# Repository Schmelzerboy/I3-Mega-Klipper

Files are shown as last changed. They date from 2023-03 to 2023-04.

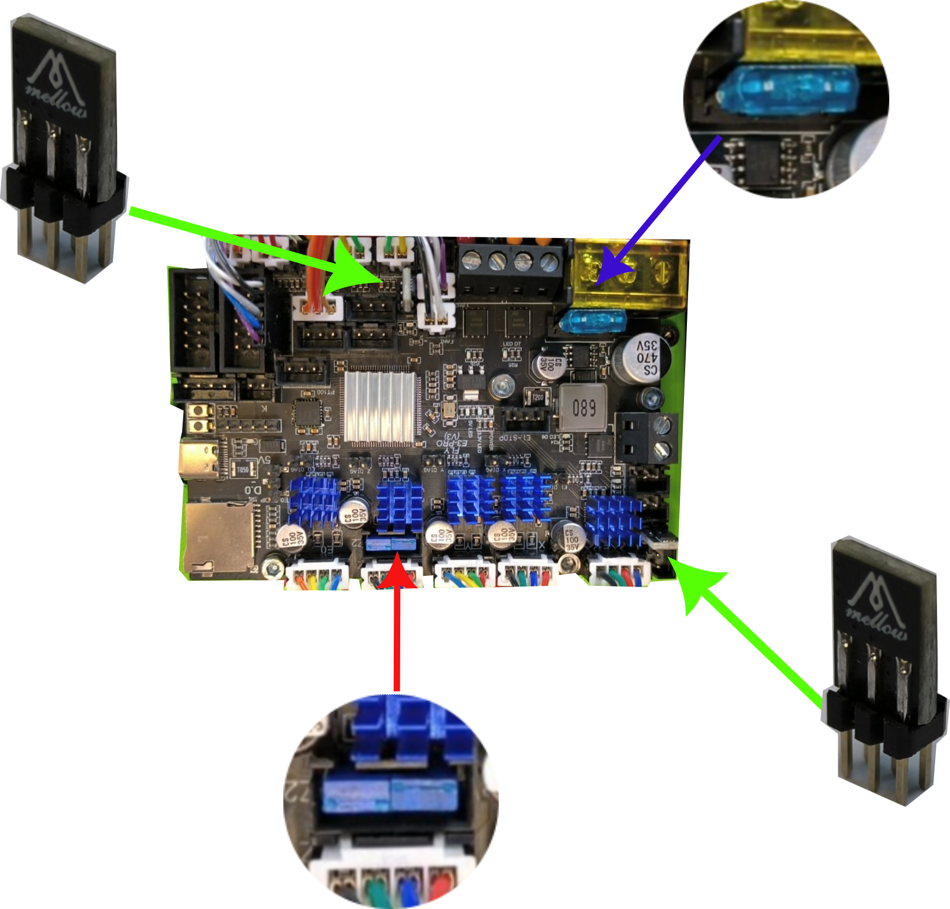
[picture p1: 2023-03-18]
Wireing Schaltplaene/Hardware_Board.png

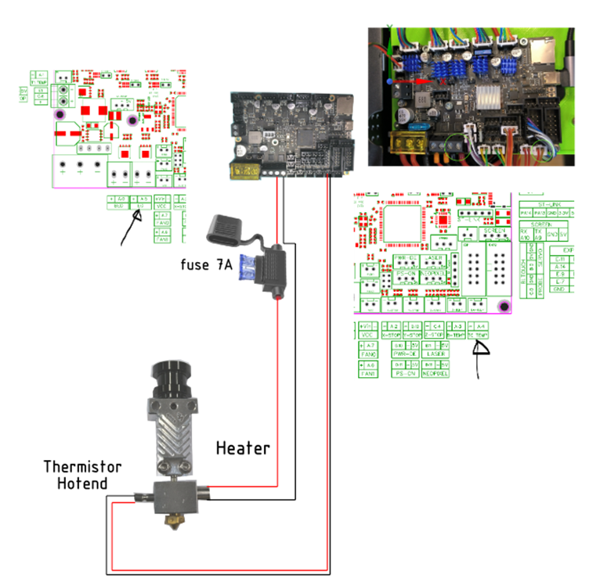
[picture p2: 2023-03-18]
Wireing Schaltplaene/hotend.PNG

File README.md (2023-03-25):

#  Anycubic I3Mega Tuning Mainsail + Klipper feat. @dr.klipper 

Video Links:  
Part 1 - https://youtu.be/kW5aFmzocZc (Anycubic I3Mega Tuning Teil 13 Mainsail + Klipper feat. @dr.klipper)  
Part 2 - https://youtu.be/CcnwJQRyG4Y (#46 - Klipper FAQ - komplette Installation)  
Part 3 - TBD

Kanal von Dr. Klipper:  
https://www.youtube.com/@dr.klipper

Mein Kanal:  
https://www.youtube.com/channel/UCTYNFDNzhLzgfR8x1OPZsGg

Mega Tuning Serie https://www.youtube.com/playlist?list=PLIsc8b5bFDG1j1bmuFCcvaNI3M9-2phBW

alle anderen Projekte:
https://www.thingiverse.com/schmelzerboy/designs

### Warnung : Ich übernehme keine Verantwortung für Schäden an Menschen oder Maschine. Der Einbau erfolgt auf eigene Gefahr. Nach Deutschen Recht dürfen nicht Elektiker keine Arbeiten an 230 Volt Netzen durchführen!

Es gelten die 5 Sicherheitsregeln:  

- Freischalten. Als Freischalten bezeichnet man das allpolige Trennen einer elektrischen Anlage von spannungsführenden Teilen.  
- Gegen Wiedereinschalten sichern.  
- Spannungsfreiheit feststellen.  
- Erden und Kurzschließen.  
- Benachbarte, unter Spannung stehende Teile abdecken oder abschranken.  

### Warning : I take no responsibility for any damage to people or machine. Installation is at your own risk. According to German law, non-electricians are not allowed to work on 230 volt networks!

The 5 safety rules apply:  

- Unlock. Disconnecting is the all-pole disconnection of an electrical system from live parts. ...
- Secure against being switched on again. ...
- determine the absence of tension. ...
- grounding and short-circuiting. ...
- Cover or fence off adjacent live parts.

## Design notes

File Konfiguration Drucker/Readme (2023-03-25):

Download:
https://github.com/Schmelzerboy/I3-Mega-Klipper

Schmelzerboy YT Kanal:
https://www.youtube.com/channel/UCTYNFDNzhLzgfR8x1OPZsGg

Dr. Klipper YT Kanal:
https://www.youtube.com/@dr.klipper

## Video Links
#> Part 1 - https://youtu.be/kW5aFmzocZc (Anycubic I3Mega Tuning Teil 13 Mainsail + Klipper feat. @dr.klipper)
#> Part 2 - https://youtu.be/CcnwJQRyG4Y (#46 - Klipper FAQ - komplette Installation)
#> Part 3 - TBD

Hier ist die Printer.cfg und Macros.cfg

Config ist mit folgenden Optionen

- BL Touch
- Mellow E3 Pro Board
- Neo Pixel
- 3 Lüfter / Hotend / Bauteillüter / Board Lüfter

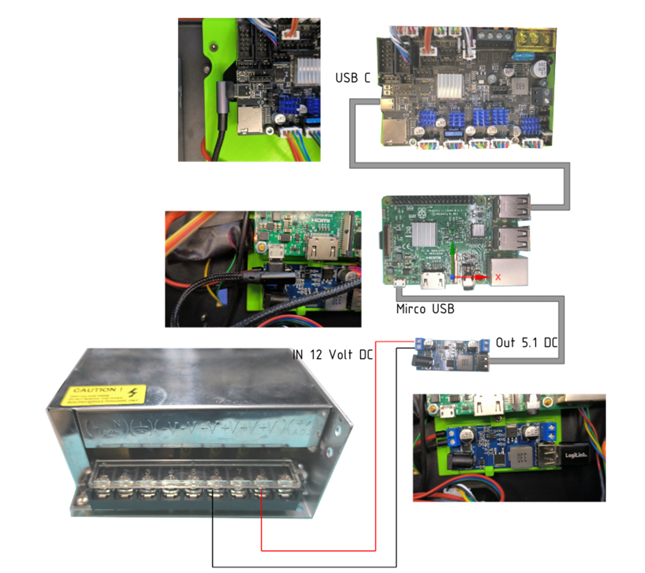
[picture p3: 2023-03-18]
Wireing Schaltplaene/DCDCWAndler.png

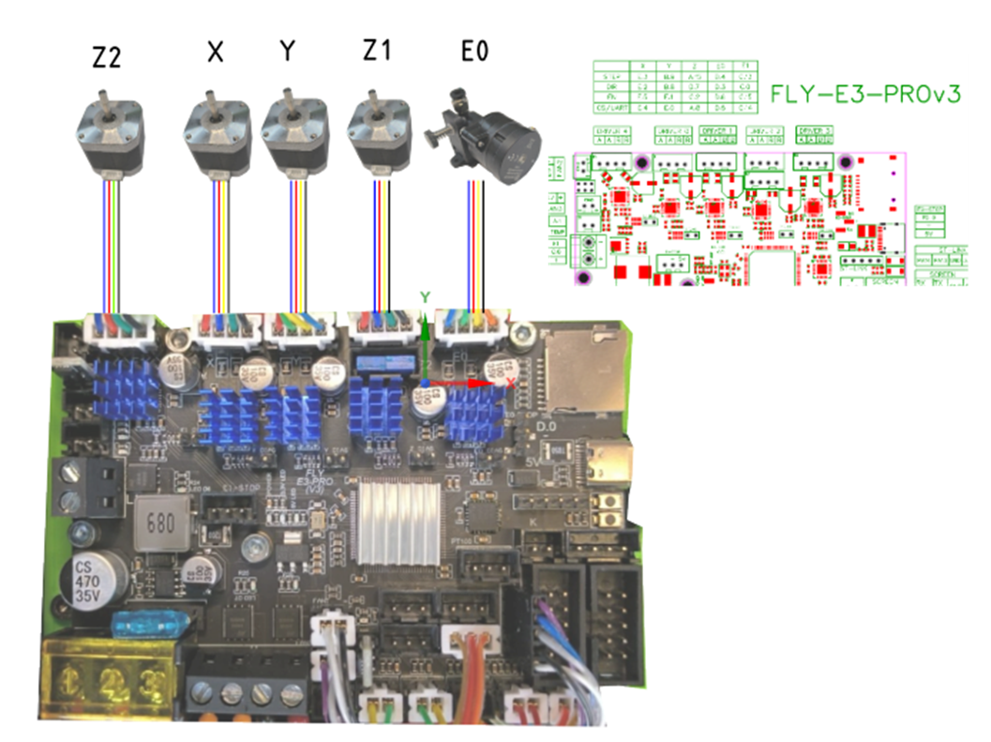
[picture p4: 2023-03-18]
Wireing Schaltplaene/Stepper.png

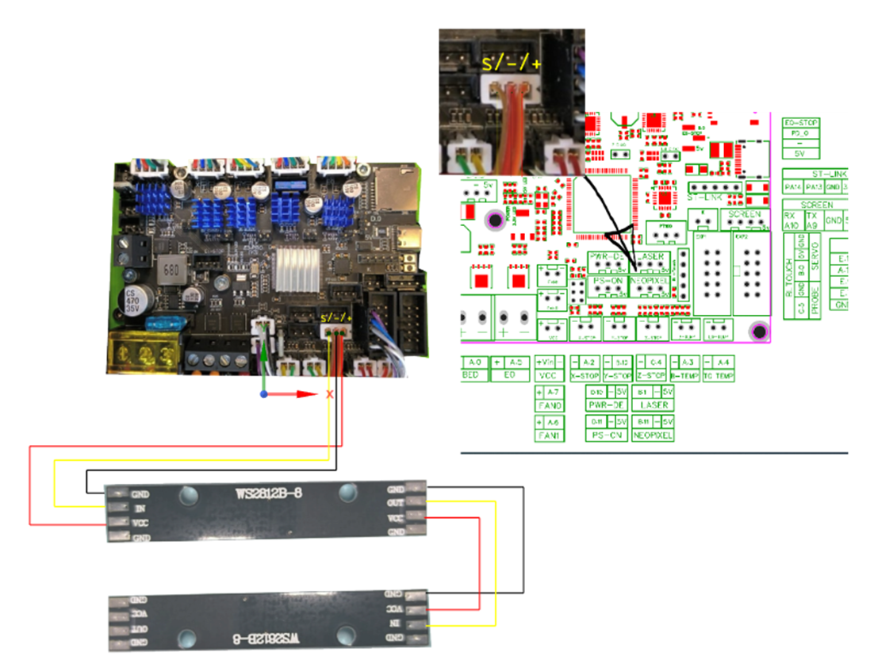
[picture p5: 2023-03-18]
Wireing Schaltplaene/neopixel.png

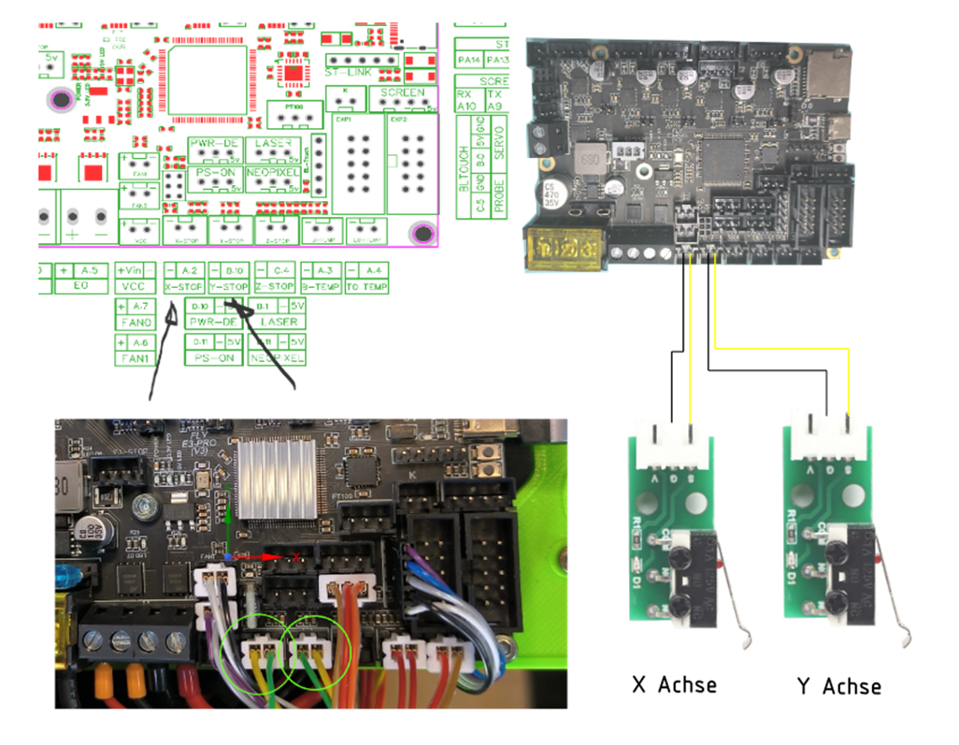
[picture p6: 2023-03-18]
Wireing Schaltplaene/Endstops.png

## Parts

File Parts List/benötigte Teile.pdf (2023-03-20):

===== Benötigte Teile =====

**NF Zone V6 12 Volt**

https://meltbro.de/nf-zone-cr10-hotend-optimiertes-hotend-fuer-ender-3-ender-5-cr-10-v6-hotend.html

**Gutscheincode "schmelzerboy"**

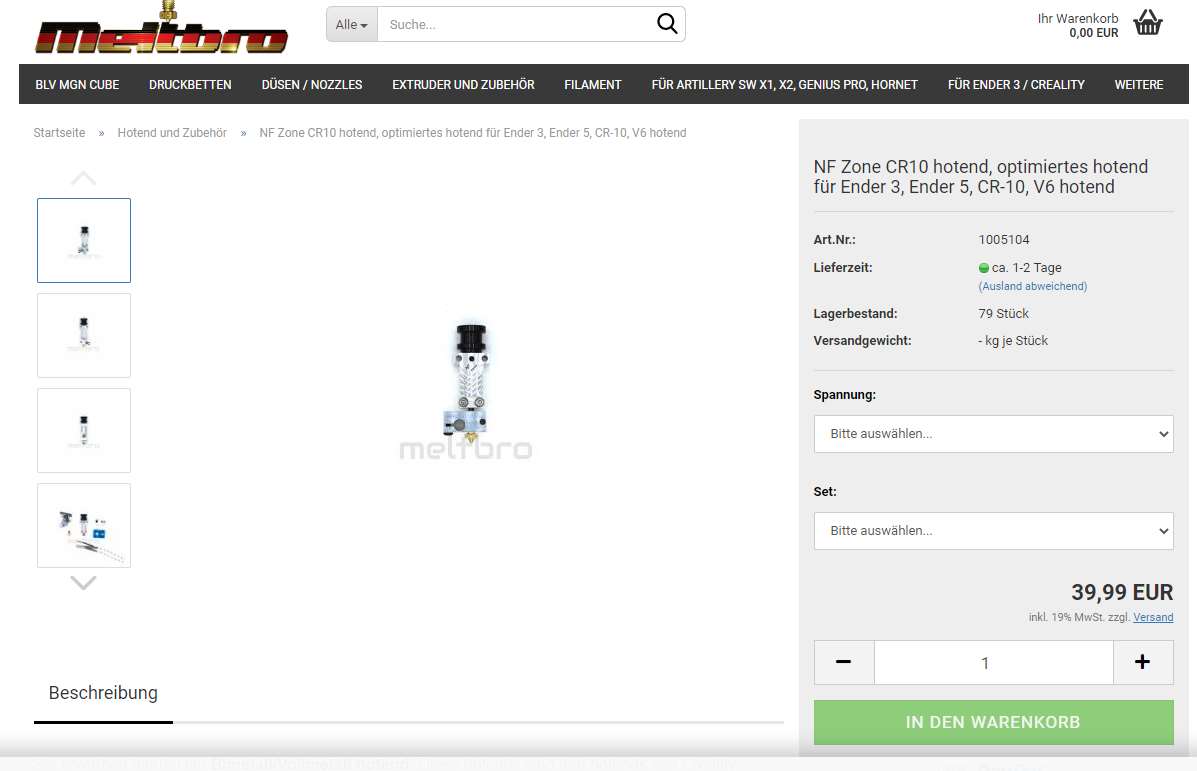
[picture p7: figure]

**Original BL Touch Sensor Nivellierung V3.1**

https://meltbro.de/original-bl-touch-nivellierungssensor-v3-1-hohe-praezision-ender-3-diydrucker.html

**Gutscheincode "schmelzerboy"**

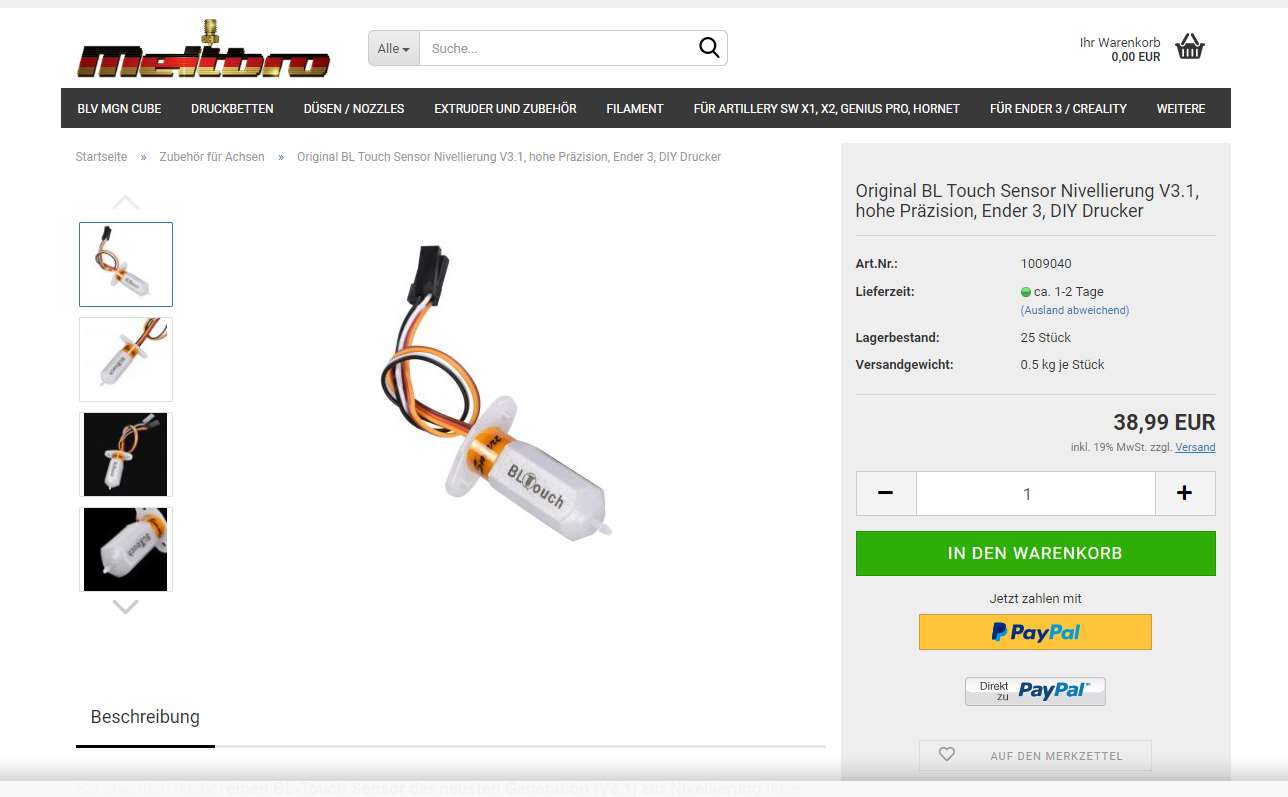
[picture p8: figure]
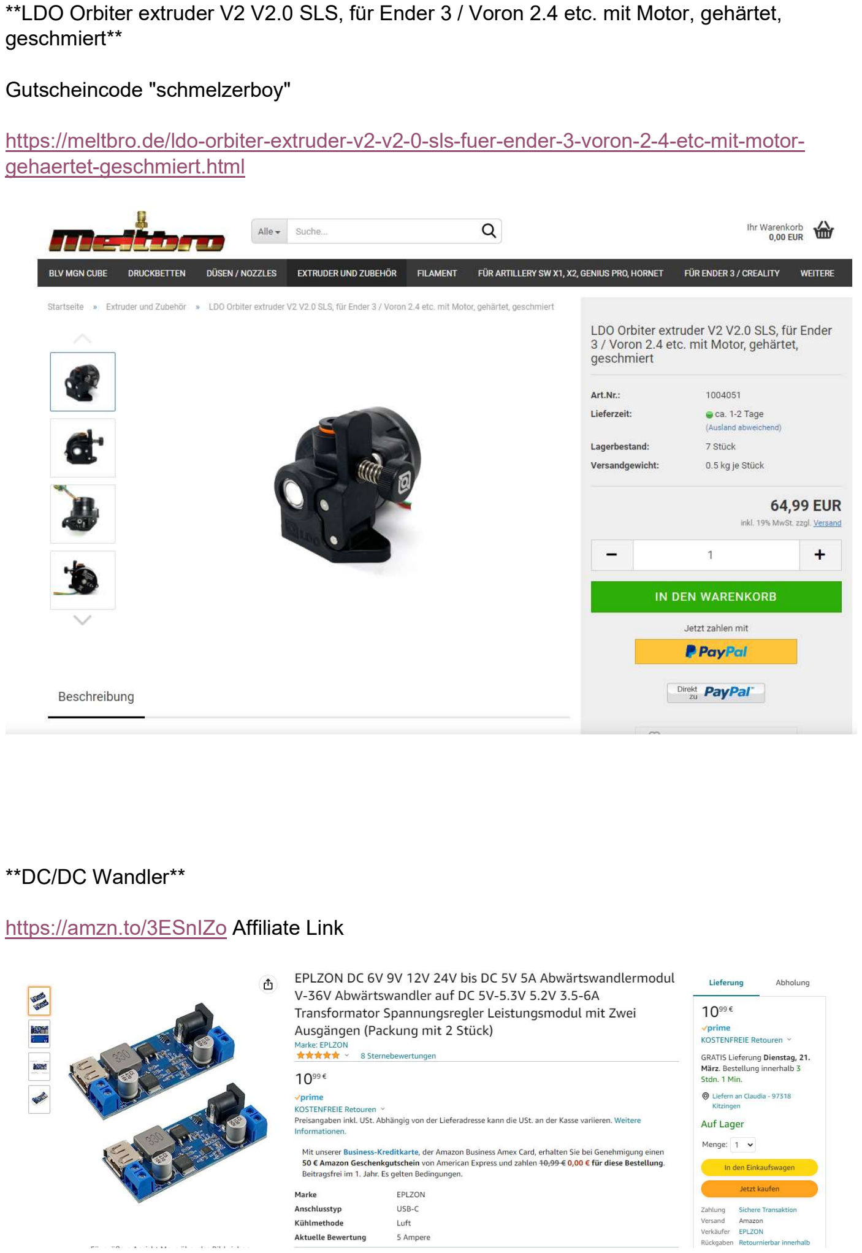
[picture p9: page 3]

**LDO Orbiter extruder V2 V2.0 SLS, für Ender 3 / Voron 2.4 etc. mit Motor, gehärtet, geschmiert**

Gutscheincode "schmelzerboy"

https://meltbro.de/ldo-orbiter-extruder-v2-v2-0-sls-fuer-ender-3-voron-2-4-etc-mit-motorgehaertet-geschmiert.html

**DC/DC Wandler**

https://amzn.to/3ESnIZo Affiliate Link

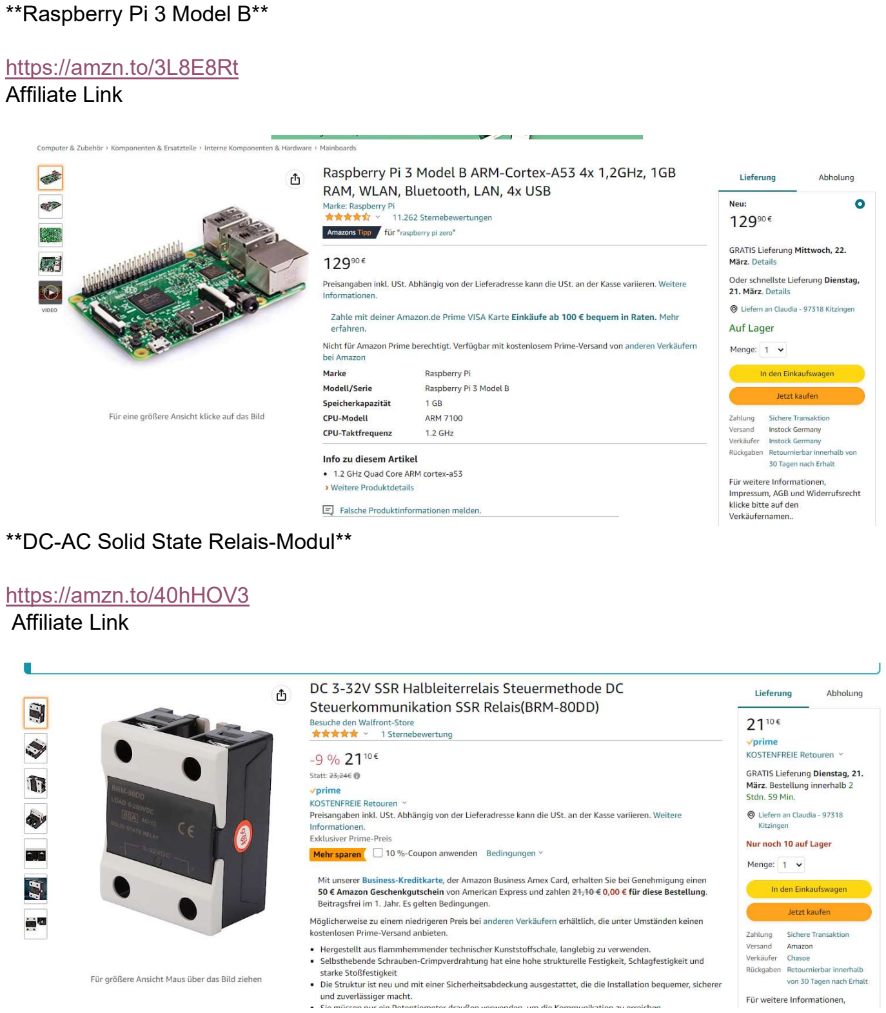
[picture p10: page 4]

**Raspberry Pi 3 Model B**

https://amzn.to/3L8E8Rt
Affiliate Link

**DC-AC Solid State Relais-Modul**

https://amzn.to/40hHOV3
Affiliate Link

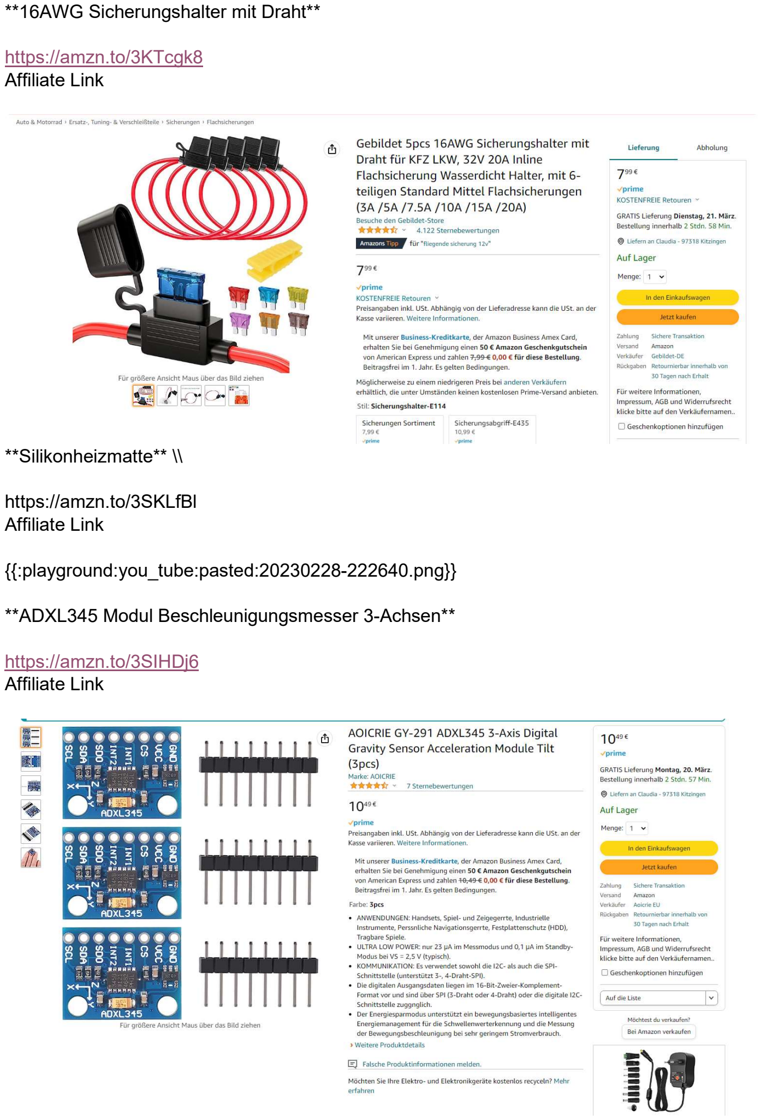
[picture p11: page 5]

**16AWG Sicherungshalter mit Draht**

https://amzn.to/3KTcgk8
Affiliate Link

**Silikonheizmatte** \\

https://amzn.to/3SKLfBl
Affiliate Link

{{:playground:you_tube:pasted:20230228-222640.png}}

**ADXL345 Modul Beschleunigungsmesser 3-Achsen**

https://amzn.to/3SIHDj6
Affiliate Link

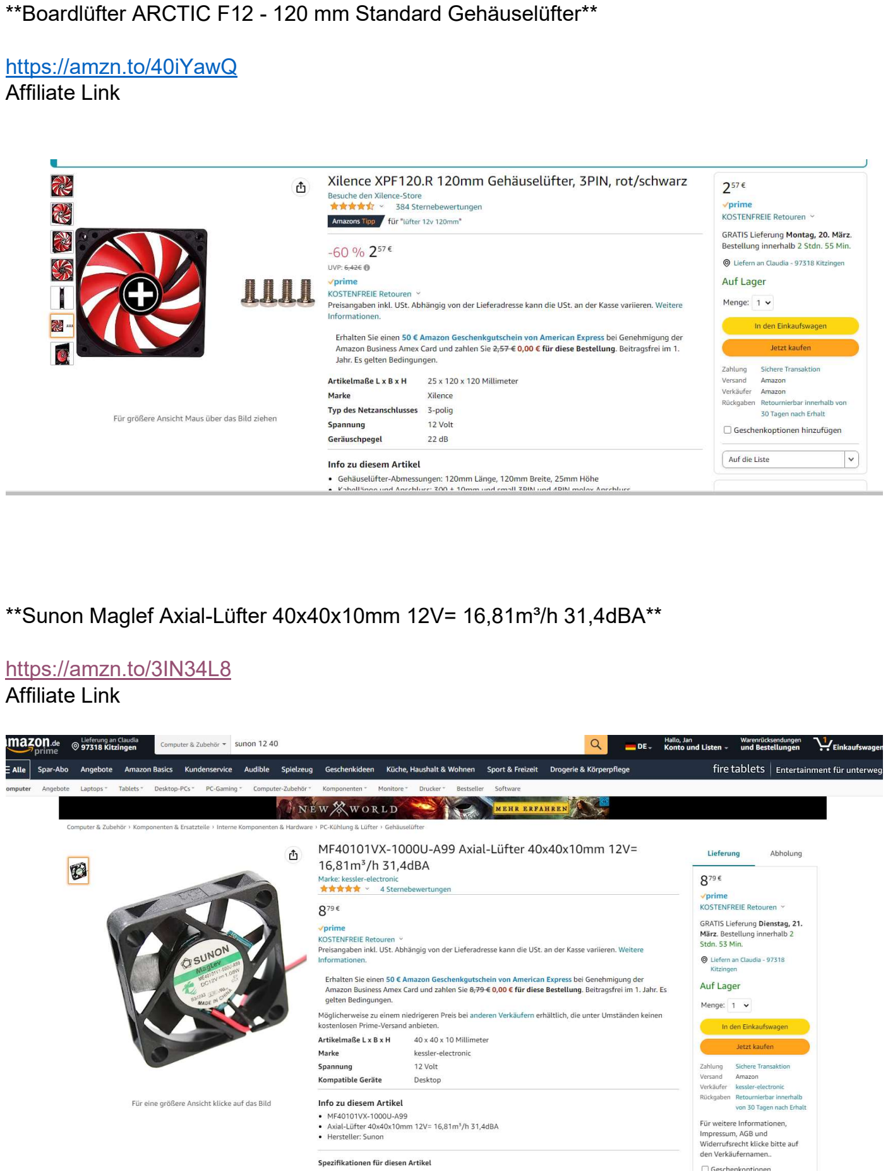
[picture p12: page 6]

**Boardlüfter ARCTIC F12 - 120 mm Standard Gehäuselüfter**

https://amzn.to/40iYawQ
Affiliate Link

**Sunon Maglef Axial-Lüfter 40x40x10mm 12V= 16,81m³/h 31,4dBA**

https://amzn.to/3IN34L8
Affiliate Link

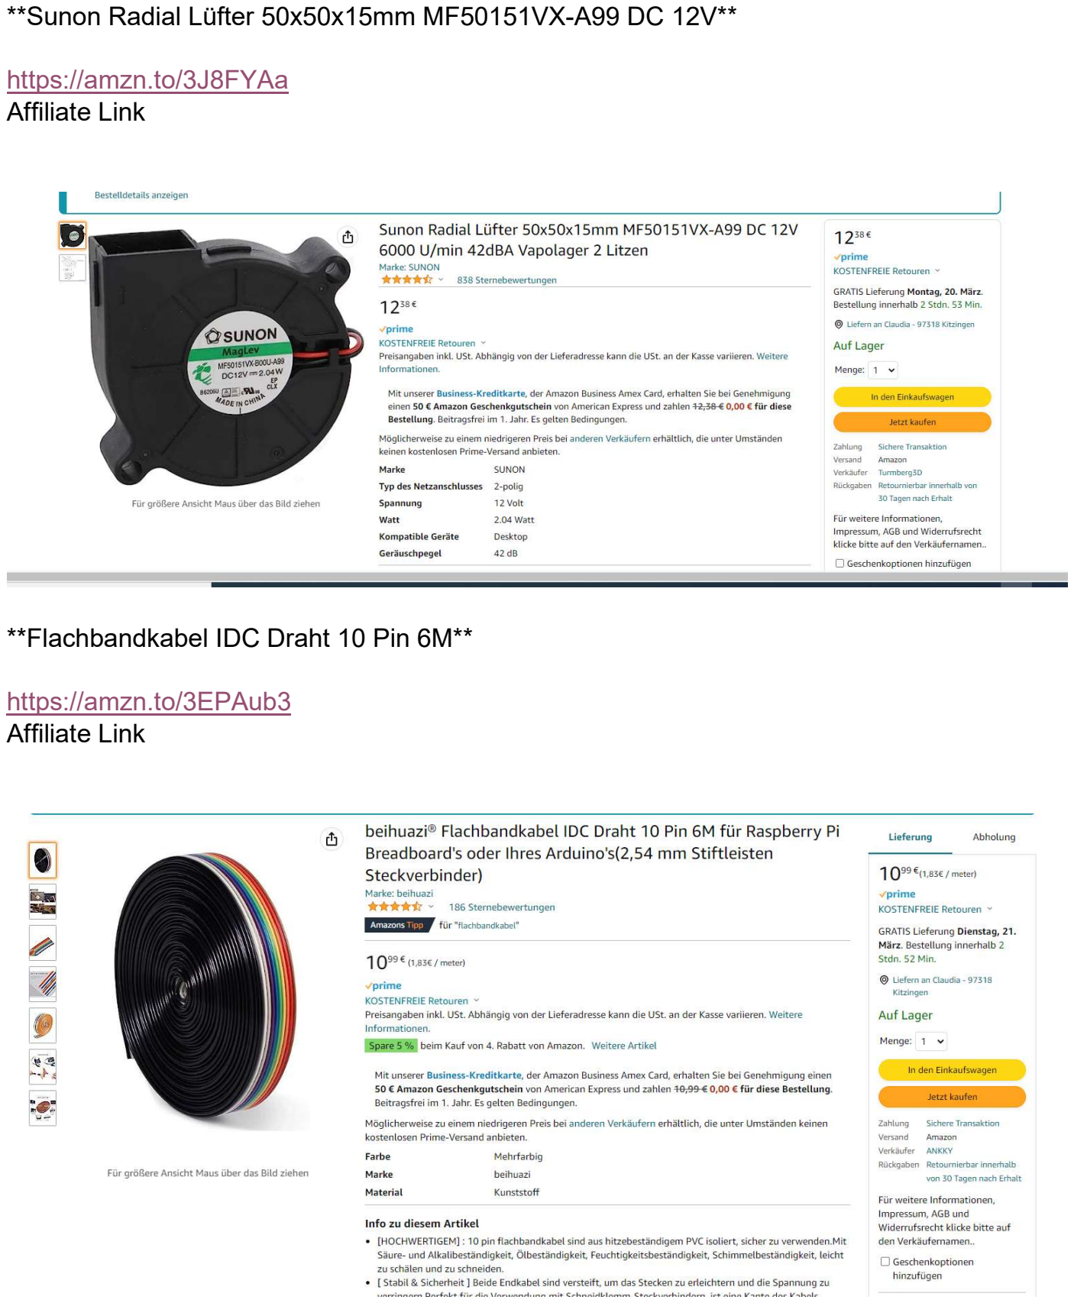
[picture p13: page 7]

**Sunon Radial Lüfter 50x50x15mm MF50151VX-A99 DC 12V**

https://amzn.to/3J8FYAa
Affiliate Link

**Flachbandkabel IDC Draht 10 Pin 6M**

https://amzn.to/3EPAub3
Affiliate Link

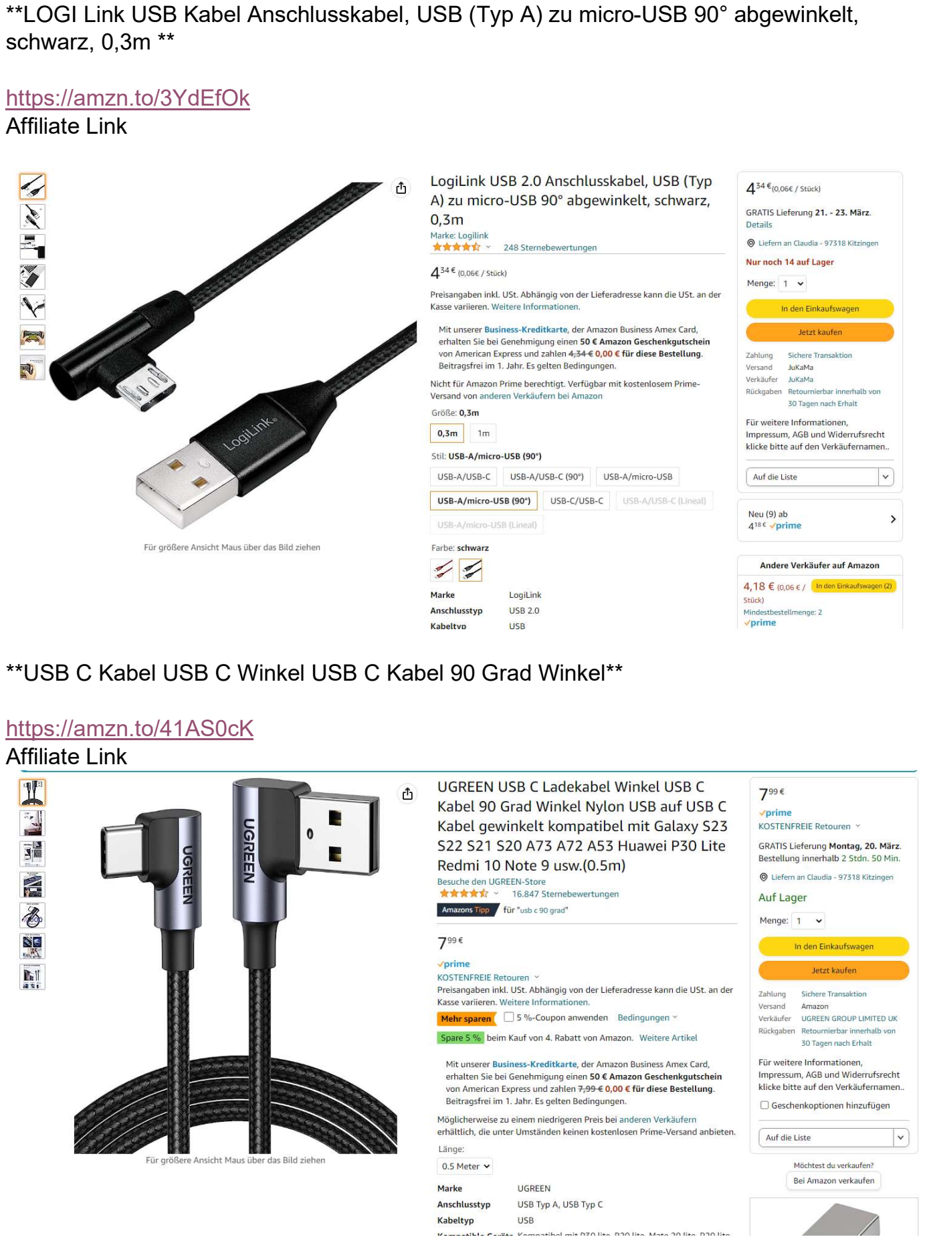
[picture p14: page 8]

**LOGI Link USB Kabel Anschlusskabel, USB (Typ A) zu micro-USB 90° abgewinkelt, schwarz, 0,3m **

https://amzn.to/3YdEfOk
Affiliate Link

**USB C Kabel USB C Winkel USB C Kabel 90 Grad Winkel**

https://amzn.to/41AS0cK
Affiliate Link

**Schrittmotorkabel 1000mm Stepper Motor Kabel**

https://amzn.to/3yPMzcP
Affiliate Link


**Heat Shrink Tubing Electric / Schrumpfschlauch**

https://amzn.to/3mfk7xX


**Werkzeug**

**Crimpzange Dupont Stecker Set - Preciva 1550 pcs 2,54 mm**

https://amzn.to/3ZCbo7h
Affiliate Link

**Lötkolben**
Affiliate Link

https://amzn.to/3IJ1Pgk


**Lötzinn**

https://amzn.to/3ZVIGPF
Affiliate Link

**Voltmeter**

https://amzn.to/3mnKEcm
Affiliate Link


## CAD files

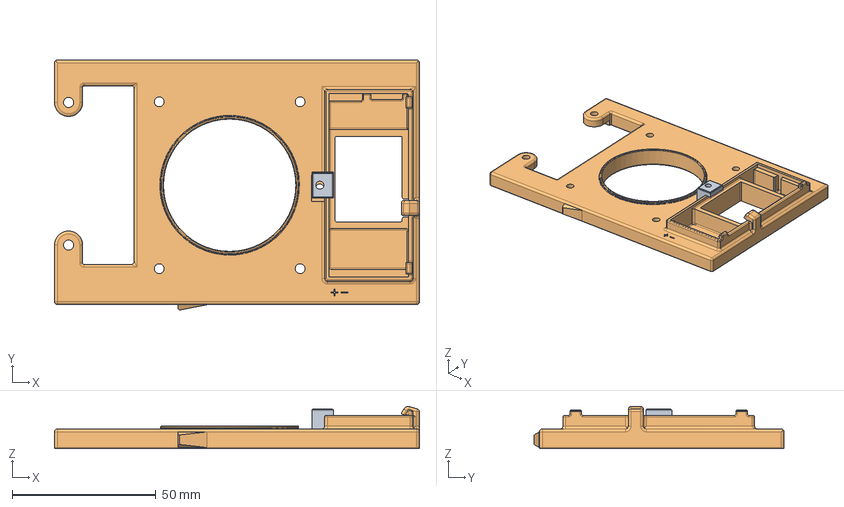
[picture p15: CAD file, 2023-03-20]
STL STEP/Pi_SSR.stp
126.9 x 87.0 x 14.6 mm
Komponente4
Volumenkörper

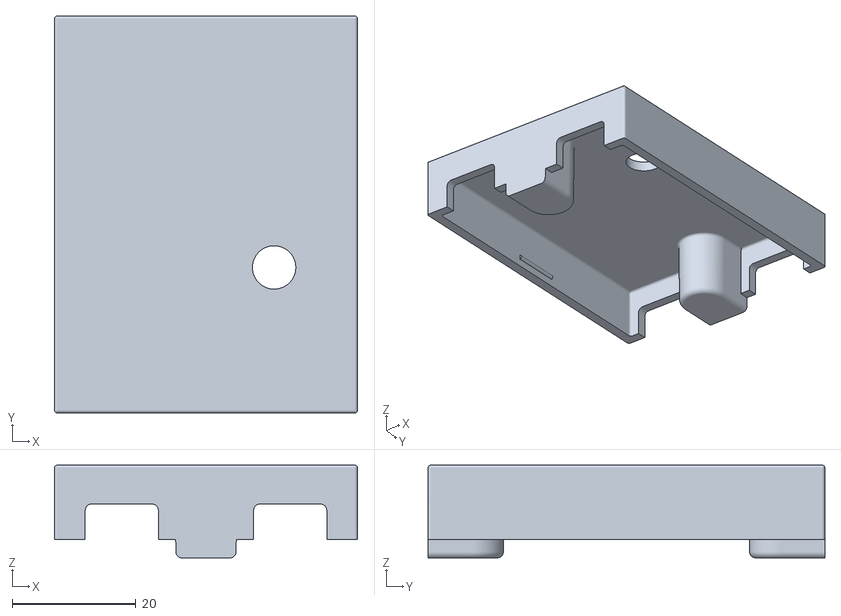
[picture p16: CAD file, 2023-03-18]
STL STEP/ssr cover.stl
49.0 x 64.1 x 15.0

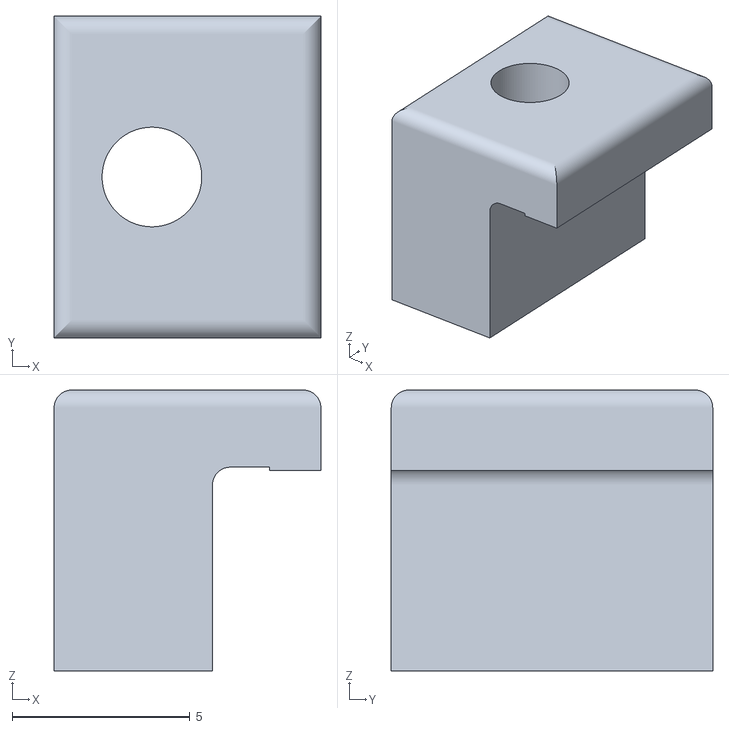
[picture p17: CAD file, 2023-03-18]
STL STEP/Pi_SSR_pusher.stl
7.50 x 9.04 x 7.90

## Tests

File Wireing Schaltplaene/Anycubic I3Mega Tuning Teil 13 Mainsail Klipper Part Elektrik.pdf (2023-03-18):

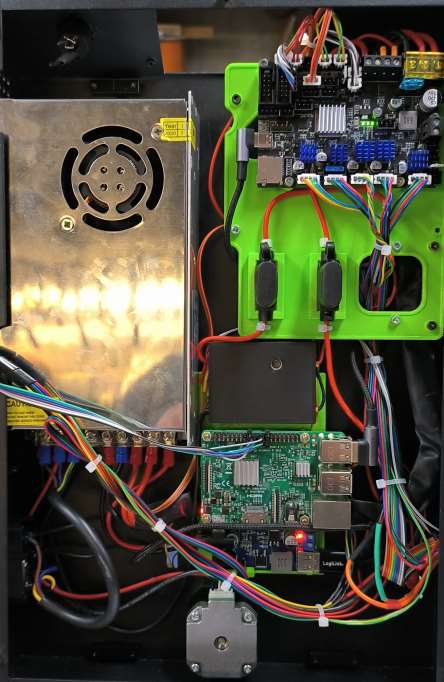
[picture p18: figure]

Download at: https://github.com/Schmelzerboy/I3-Mega-Klipper

### 1 Schmelzdoku Mainsail Klipper

# Anycubic I3Mega Tuning Teil 13 Mainsail Klipper Part: Elektrik

Warning : I take no responsibility for any damage to people or machine. The installation takes place at risk.
Warung : Ich übernehme keine Verantwortung für Schäden an Menschen oder Maschine. Der Einbau erfolgt auf eigene Gefahr.

### 2 Schmelzdoku Mainsail Klipper

Board Mellow E3 ProV3 Doku:

https://teamgloomy.github.io/fly_e3_pro_v3_general.html

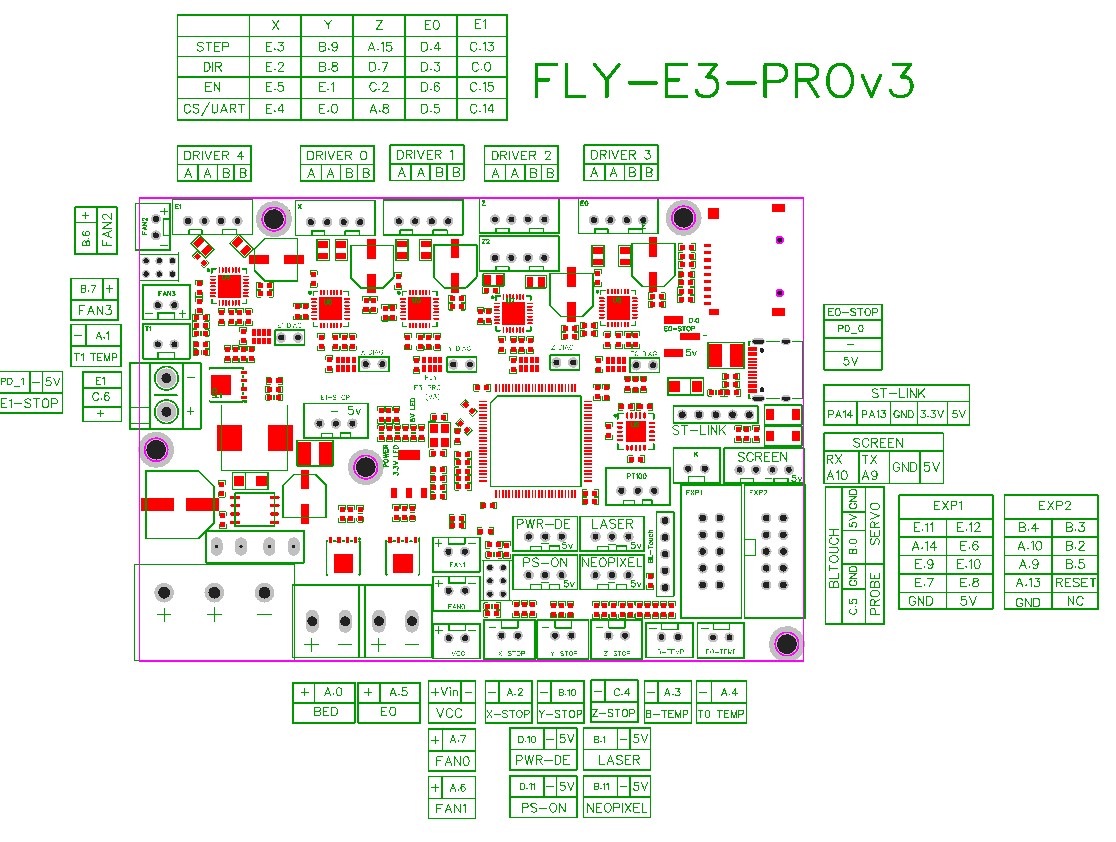
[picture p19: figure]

### 3 Schmelzdoku Mainsail Klipper

### 1. Board Settings

- blue 10A fuse
- green fan mosfet
- red jumper Z- Axis

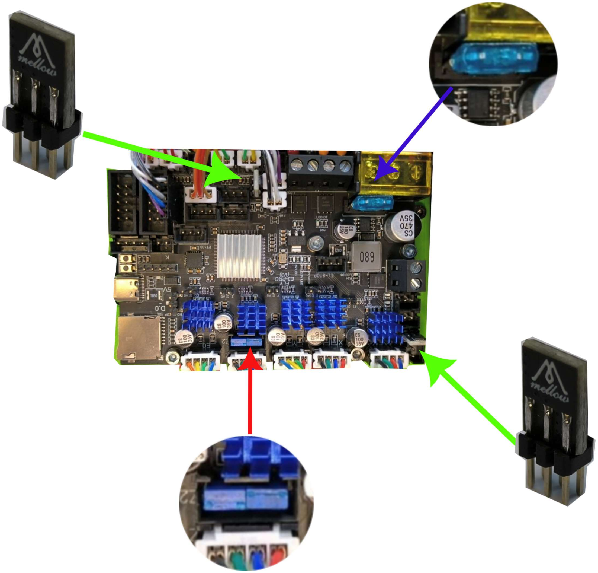
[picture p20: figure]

2. [fan]

### 4 Schmelzdoku Mainsail Klipper

- Fan 0 pin: PA7 [fan]
- Fan 1 pin: PA6 [heater fan]
- Fan 3 pin: PB7 [controller_fan]

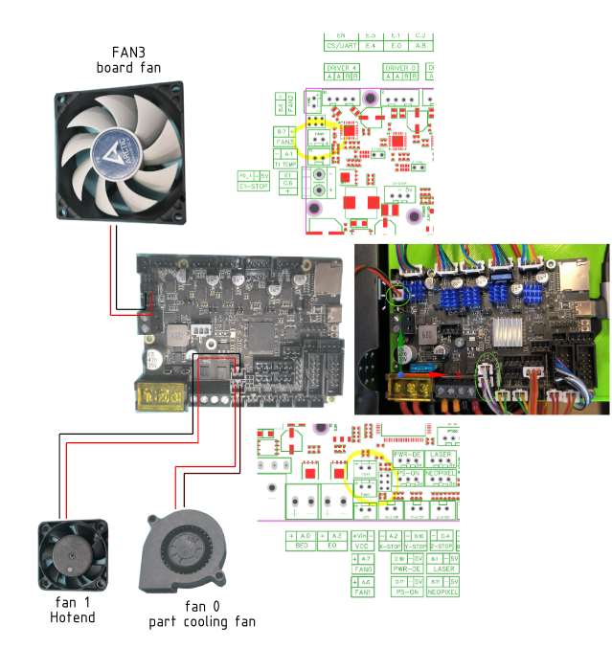
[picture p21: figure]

### 3. Power Supply Board

### 5 Schmelzdoku Mainsail Klipper

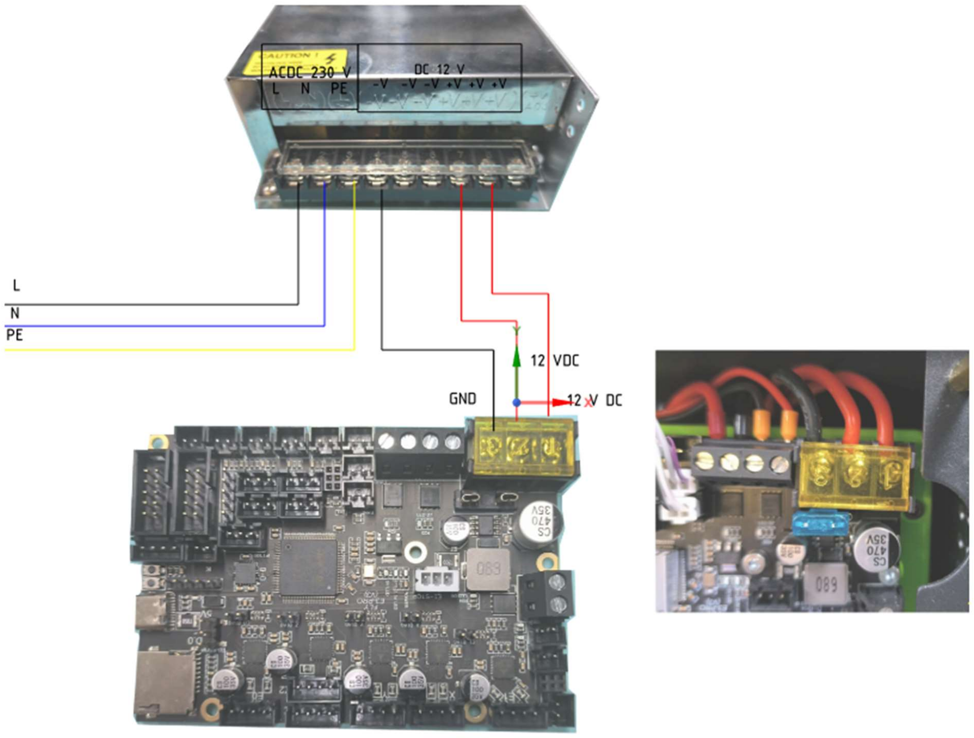
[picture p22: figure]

4. [heater_bed]

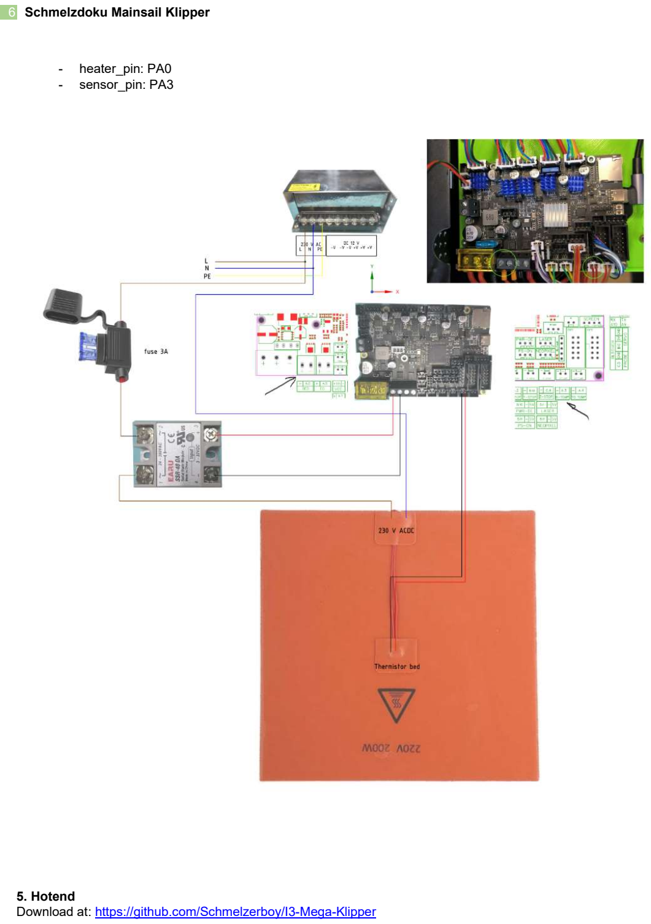
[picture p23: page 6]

### 6 Schmelzdoku Mainsail Klipper

- heater_pin: PA0
- sensor_pin: PA3

### 5. Hotend

### 7 Schmelzdoku Mainsail Klipper

heater_pin: PA5
sensor_pin: PA4

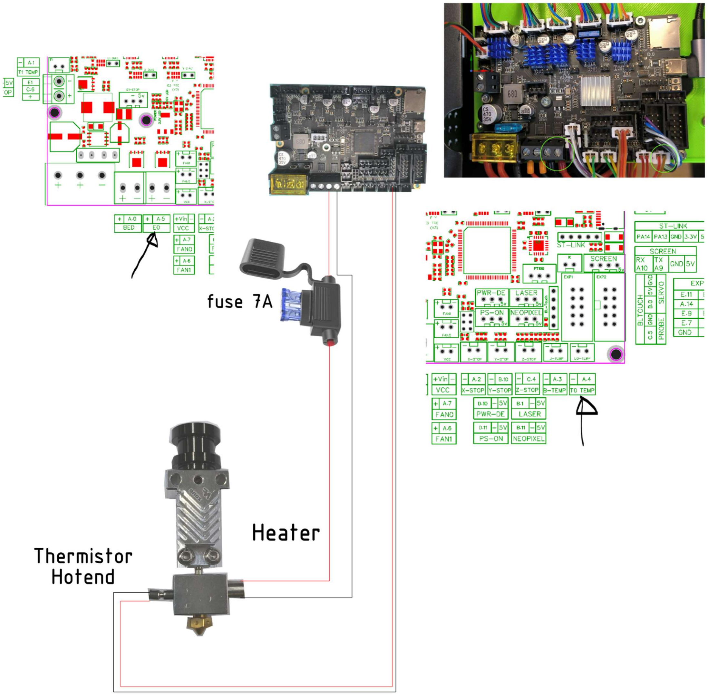
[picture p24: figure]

### 6. Stepper

### 8 Schmelzdoku Mainsail Klipper

[stepper_x] | step_pin: PE3 dir_pin: PE2 enable_pin: !PE5
[stepper_y] | step_pin: PB3 dir_pin: PB8 enable_pin: !PE1
[stepper_z] | step_pin: PA15 dir_pin: PD7 enable_pin: !PC2
[stepper_z1] | step_pin: PC13 dir_pin: PC0 enable_pin: !PC15
[extruder] | step_pin: PD4 dir_pin: PD3 enable_pin: !PD6

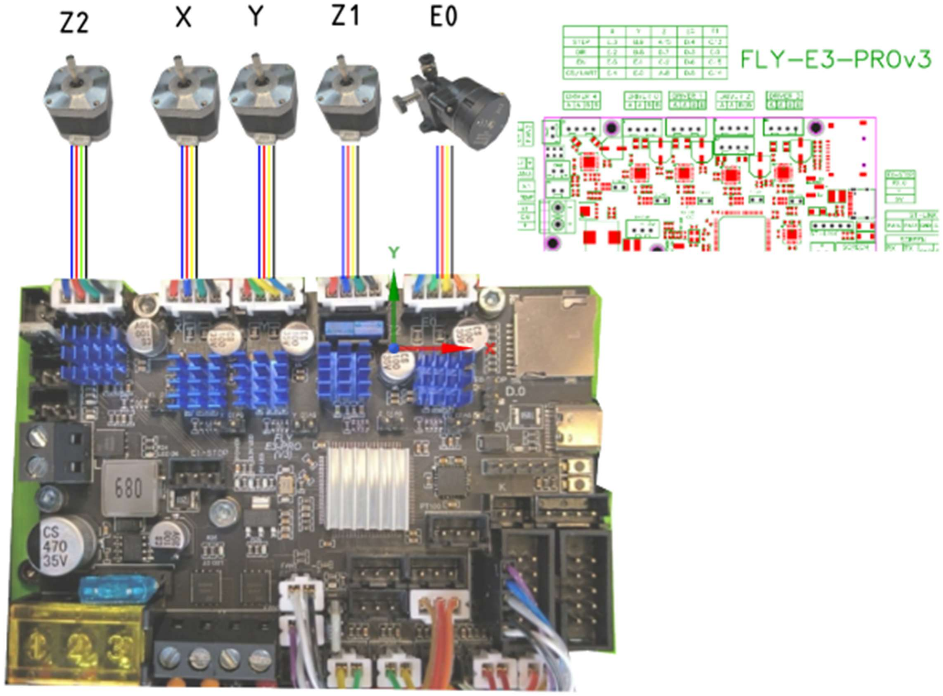
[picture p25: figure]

6. [bltouch]

### 9 Schmelzdoku Mainsail Klipper

sensor_pin: ^PC5
control_pin: PB0

Check:
https://teamgloomy.github.io/fly_e3_pro_v3_bltouch.html

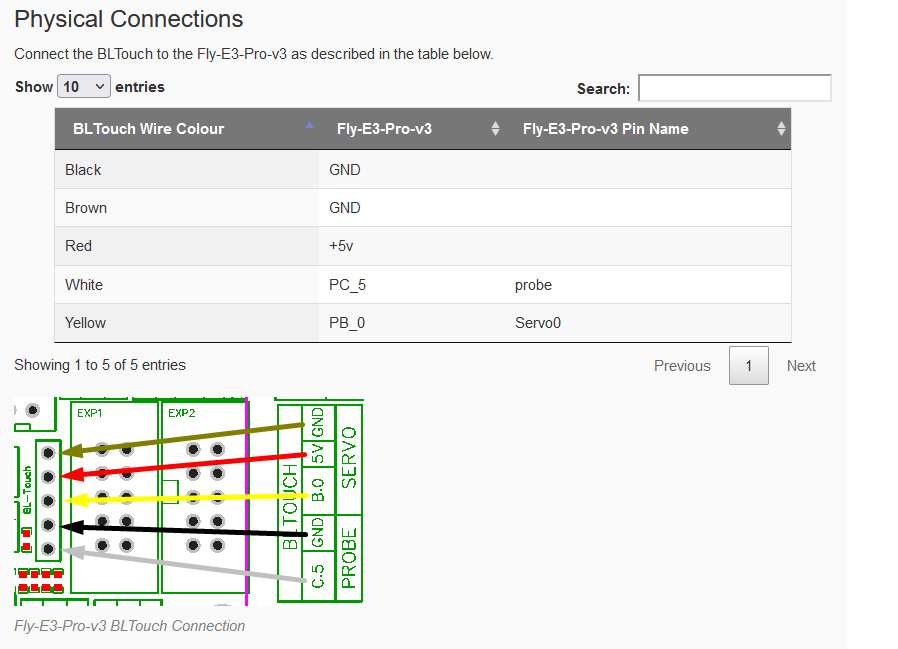
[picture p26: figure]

### 7. Endstops

### 10 Schmelzdoku Mainsail Klipper

X = endstop_pin: !PA2
Y= endstop_pin: !PB10

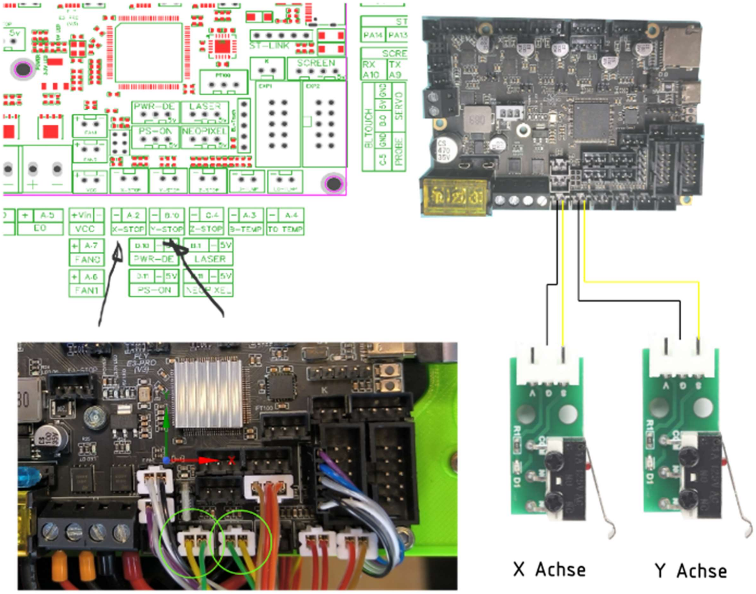
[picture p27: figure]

### 11 Schmelzdoku Mainsail Klipper

8. [ADXL]

cs_pin: rpi:None

9 . DC/DC Wandler / USB Verkabelung


### 12 Schmelzdoku Mainsail Klipper

10. [neopixel Leds]


### 13 Schmelzdoku Mainsail Klipper

pin : PB11

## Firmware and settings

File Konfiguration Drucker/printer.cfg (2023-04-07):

## Master Link für alle Anleitungen / Printer.cfg / macros:
## https://github.com/Schmelzerboy/I3-Mega-Klipper
##
## Printer Anycuic I3 Mega MK4 THE REAL ORBITER KLIPPER Version
# Projekt wurde erstellt von:
#  Jan Oerter      (YT Schmelzerboy) ###https://www.youtube.com/channel/UCTYNFDNzhLzgfR8x1OPZsGg
#  Dominik Schmidt (YT Dr. KLipper)  ###https://www.youtube.com/@dr.klipper

## Default Compile Settings
#> CanBoot (https://github.com/Arksine/CanBoot)
#      Micro-controller Architecture (STMicroelectronics STM32)  --->
#      Processor model (STM32F407)  --->
#      Build CanBoot deployment application (32KiB bootloader)  --->
#      Clock Reference (8 MHz crystal)  --->
#      Communication interface (USB (on PA11/PA12))  --->
#      Application start offset (32KiB offset)  --->
#      USB ids  --->
#  ()  GPIO pins to set on bootloader entry
#  [*] Support bootloader entry on rapid double click of reset button
#  [ ] Enable bootloader entry on button (or gpio) state
#  [ ] Enable Status LED
#
#> Klipper 
#  [*] Enable extra low-level configuration options
#      Micro-controller Architecture (STMicroelectronics STM32)  --->
#      Processor model (STM32F407)  --->
#      Bootloader offset (32KiB bootloader)  --->
#      Clock Reference (8 MHz crystal)  --->
#      Communication interface (USB (on PA11/PA12))  --->
#      USB ids  --->
#  ()  GPIO pins to set at micro-controller startup

## Video Links
## Installation / Einrichtung
#> Part 1 - https://youtu.be/kW5aFmzocZc (Anycubic I3Mega Tuning Teil 13 Mainsail + Klipper feat. @dr.klipper)
#> Part 2 - https://youtu.be/CcnwJQRyG4Y (#46 - Klipper FAQ - komplette Installation)
#> Part 3 - TBD

#> Demo Video:
##> https://youtu.be/m_DZtZd5RRo (Anycubic I3 Mega "Der Einstiegsdrucker" kann 30 min. Benchy drucken?)

## Wichtige Links:
## Mellow FLY-E3 Pro V3:
## Pinout E3 Pro V3 https://teamgloomy.github.io/fly_e3_pro_v3_pins.html
## Ellis Prining Guide:
## https://ellis3dp.com/Print-Tuning-Guide/


#########################################
## Incluide
#########################################
[include mainsail.cfg]
[include macros.cfg]
#[include calibrate.cfg]      #https://book.cryd.de/books/klipper/page/youtube-kalibrierungsmakro
#[include shell_command.cfg]  #https://book.cryd.de/books/klipper/page/youtube-kalibrierungsmakro
[exclude_object]
[respond]


#########################################
## MCU Config
## https://www.klipper3d.org/Config_Reference.html#mcu
## Hint: Get all serial ports with links in Linux: 
## ls -lR /dev/ | grep -v '\->\s../tty' | grep -e 'tty[[:alpha:]]' -e serial
#########################################
[mcu]
serial                  : /dev/serial/by-id/usb-Klipper_stm32f407xx_28002C000E47393438343535-if00

## Uncomment this part if you use the Raspberry Pi MCU
## > https://www.klipper3d.org/RPi_microcontroller.html
[mcu rpi] 
serial                  : /tmp/klipper_host_mcu


#########################################
## Printer Config
## https://www.klipper3d.org/Config_Reference.html#printer
## https://www.klipper3d.org/Resonance_Compensation.html?h=selec#selecting-max_accel
#########################################
[printer]
kinematics              : cartesian
max_velocity            : 400
max_accel               : 4500
max_accel_to_decel      : 2250
max_z_velocity          : 15
max_z_accel             : 300
square_corner_velocity  : 10


#########################################
## Stepper
## https://www.klipper3d.org/Config_Reference.html#stepper
#########################################
[stepper_x]
step_pin                : PE3
dir_pin                 : PE2
enable_pin              : !PE5
microsteps              : 16
rotation_distance       : 40
endstop_pin             : !PA2
position_endstop        : 0
position_max            : 220
homing_speed            : 80

[tmc2209 stepper_x]
uart_pin                : PE4
run_current             : 1.1
interpolate             : False

[stepper_y]
step_pin                : PB9
dir_pin                 : !PB8
enable_pin              : !PE1
microsteps              : 16
rotation_distance       : 40
endstop_pin             : !PB10
position_endstop        : 0
position_max            : 209
homing_speed            : 80

[tmc2209 stepper_y]
uart_pin                : PE0
run_current             : 1.3
interpolate             : False

[stepper_z]
step_pin                : PA15
dir_pin                 : !PD7
enable_pin              : !PC2
microsteps              : 16
full_steps_per_rotation : 200
rotation_distance       : 8
endstop_pin             : probe:z_virtual_endstop
position_max            : 180

[tmc2209 stepper_z]
uart_pin                : PA8
run_current             : 0.800
interpolate             : False
 
[stepper_z1]
step_pin                : PC13
dir_pin                 : !PC0
enable_pin              : !PC15
microsteps              : 16
full_steps_per_rotation : 200
rotation_distance       : 8
endstop_pin             : probe:z_virtual_endstop

[tmc2209 stepper_z1]
uart_pin                : PC14
run_current             : 0.800
interpolate             : False


#########################################
## Extruder Config
## https://www.klipper3d.org/Config_Reference.html#extruder
#########################################
[extruder]
step_pin                  : PD4
dir_pin                   : !PD3
enable_pin                : !PD6
microsteps                : 16
rotation_distance         : 4.70448   #https://www.klipper3d.org/Rotation_Distance.html
nozzle_diameter           : 0.400
filament_diameter         : 1.750
heater_pin                : PA5
sensor_pin                : PA4
sensor_type               : ATC Semitec 104GT-2 # https://www.klipper3d.org/Config_Reference.html#common-thermistors
pullup_resistor           : 2200        #pullup_resistor: standard 4700 E3-Pro: 2200
#control                   : pid        # https://www.klipper3d.org/G-Codes.html?h=pid#pid_calibrate_1
#pid_Kp                    : 26.131
#pid_Ki                    : 1.124
#pid_Kd                    : 151.884
min_temp                  : 0
max_temp                  : 280
max_extrude_cross_section : 25
max_extrude_only_distance : 120
pressure_advance          : 0.0414                 #https://www.klipper3d.org/Pressure_Advance.html
min_extrude_temp          : 150

[tmc2209 extruder]
uart_pin                  : PD5
run_current               : 0.720
interpolate               : False


#########################################
## Bed Config
## https://www.klipper3d.org/Config_Reference.html#heater_bed
#########################################
[heater_bed]
heater_pin                : PA0
sensor_pin                : PA3
# https://www.klipper3d.org/Config_Reference.html#common-thermistors
sensor_type               : ATC Semitec 104GT-2
pullup_resistor           : 2200       #pullup_resistor: standard 4700 E3-Pro: 2200
#control                   : pid
#pid_Kp                    : 58.231       #https://www.klipper3d.org/G-Codes.html?h=pid#pid_calibrate_1
#pid_Ki                    : 1.109
#pid_Kd                    : 764.282
min_temp                  : 0
max_temp                  : 110


#########################################
## Fans
## https://www.klipper3d.org/Config_Reference.html#fans
#########################################
## Fan0 (A.7)
[fan]  
pin                       : PA7
#cycle_time                : 0.50

## Fan1 (A.6)
[heater_fan E0]
pin: PA6
#cycle_time                :
heater                    : extruder
heater_temp               : 50.0
fan_speed                 : 1.0

## Board Fan (B.7)
[controller_fan my_controller_fan]
pin: PB7



#########################################
## Bed Mesh
## https://www.klipper3d.org/Config_Reference.html#bed_mesh
#########################################
[bed_mesh]
speed                      : 150
horizontal_move_z          : 8
mesh_min                   : 32, 15
mesh_max                   : 200, 196
probe_count                : 6,6
#fade_start                 : 1.0
#mesh_pps                   : 2,3
algorithm                  : bicubic
bicubic_tension            : 0.2
relative_reference_index   : 18


########################################
## Z Tilt
## This feature enables independent adjustment of multiple z steppers to adjust for tilt
## https://www.klipper3d.org/Config_Reference.html#z_tilt
########################################
[z_tilt]
z_positions                :
                             -65,105
                             285,105    
points                     :
                             0,130
                             163,130
speed                      : 100
horizontal_move_z          : 10
retries                    : 5
retry_tolerance            : 0.02
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

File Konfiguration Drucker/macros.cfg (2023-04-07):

## Master Link für alle Anleitungen / Printer.cfg / macros:
## https://github.com/Schmelzerboy/I3-Mega-Klipper
##
## Printer Anycuic I3 Mega MK4 THE REAL ORBITER KLIPPER Version
# Projekt wurde erstellt von:
#  Jan Oerter      (YT Schmelzerboy) ###https://www.youtube.com/channel/UCTYNFDNzhLzgfR8x1OPZsGg
#  Dominik Schmidt (YT Dr. KLipper)  ###https://www.youtube.com/@dr.klipper

## Default Compile Settings
#> CanBoot (https://github.com/Arksine/CanBoot)
#      Micro-controller Architecture (STMicroelectronics STM32)  --->
#      Processor model (STM32F407)  --->
#      Build CanBoot deployment application (32KiB bootloader)  --->
#      Clock Reference (8 MHz crystal)  --->
#      Communication interface (USB (on PA11/PA12))  --->
#      Application start offset (32KiB offset)  --->
#      USB ids  --->
#  ()  GPIO pins to set on bootloader entry
#  [*] Support bootloader entry on rapid double click of reset button
#  [ ] Enable bootloader entry on button (or gpio) state
#  [ ] Enable Status LED
#
#> Klipper 
#  [*] Enable extra low-level configuration options
#      Micro-controller Architecture (STMicroelectronics STM32)  --->
#      Processor model (STM32F407)  --->
#      Bootloader offset (32KiB bootloader)  --->
#      Clock Reference (8 MHz crystal)  --->
#      Communication interface (USB (on PA11/PA12))  --->
#      USB ids  --->
#  ()  GPIO pins to set at micro-controller startup

## Video Links
## Installation / Einrichtung
#> Part 1 - https://youtu.be/kW5aFmzocZc (Anycubic I3Mega Tuning Teil 13 Mainsail + Klipper feat. @dr.klipper)
#> Part 2 - https://youtu.be/CcnwJQRyG4Y (#46 - Klipper FAQ - komplette Installation)
#> Part 3 - TBD

#> Demo Video:
##> https://youtu.be/m_DZtZd5RRo (Anycubic I3 Mega "Der Einstiegsdrucker" kann 30 min. Benchy drucken?)

## Wichtige Links:
## Mellow FLY-E3 Pro V3:
## Pinout E3 Pro V3 https://teamgloomy.github.io/fly_e3_pro_v3_pins.html
## Ellis Prining Guide:
## https://ellis3dp.com/Print-Tuning-Guide/

################################################
## PRINT_START T_EXTRUDER= T150_BED=50
################################################

[gcode_macro START_PRINT]
gcode:
 
    {% set T_BED = params.TEMP_BED|default(60)|int %}
    {% set T_EXTRUDER = params.TEMP_EXTRUDER|default(200)|float %}
    LED_off                                  ; LED OFF
    M83                                      ; Set relative Extrusion
    LED_Homing                               ; HOME LED
    _CG28                                    ; Home                           
    LED_Heating                              ; LED HEATING
    _PREHEAT                                  ; PREHEAT Bed and Nozzle
    {% if printer.heater_bed.temperature <= 50 %}                            
    RESPOND MSG="Start Preheating Phase...."
    {% endif %}
    M140 S{T_BED}                            ; Bed heat up temp
    M190 S{T_BED}                            ; Wait for Bed heat up
    RESPOND MSG="Start Z-Tilt Adjust...."
    LED_Homing                               ; LED HOMING
    Z_TILT_ADJUST                            ; Adjust Z axes
    LED_Heating                              ; LED HEATING
    G1 X0 Y200 Z30 F6000
    RESPOND MSG="PREHEAT now ist time to clean the Bed"
    M104 S{T_EXTRUDER}                       ; Extruder heat up temp
    M109 S{T_EXTRUDER}                       ; Extruder heat up to target temp
    LED_Homing                               ; LED HOMING
    RESPOND MSG="Final Z Homing"
    G91                                      ; Relative Positionierung
    G1 E-3 F6000                             ; zieh Extruder zurck
    G90                                      ; absolut Positionierung
    G1 X83 Y117 F6000                        ; fahre auf Home XY
    G28   Z                                  ; Home Z final
    BED_MESH_PROFILE LOAD=PLA60              ; Load Mesh  
    #G0 Z5                                   ; Lift nozzle a bit
    M107                                     ; start with the fan off
    G92 E0.0                                 ; Reset extruder length
    RESPOND MSG="Start Primline...."
    PRIME_LINE                               ; Prime Line
    LED_Printing                             ; LED Printing


[gcode_macro END_PRINT]
gcode:
  TURN_OFF_HEATERS
  LED_off                            ; LED OFF
  G91                                ; Relative Positionierung
  G1 E-3 F6000                       ; Retract
  G1 X-0.5 Y-0.5 Z5 E-5  F6000          
  G90                                ; Absolute Positionierung
  G1 X0 Y209 F3000                   ; Bewege den Kopf nach hinten in die Mitte
  M107                               ; Partcooling Fan deaktivieren
                        
  RESPOND MSG="Print Finish"
  M117 Print done

[gcode_macro PRIME_LINE]
gcode:
  G90                                ; Absolute Positionierung
  G1 Z5 F8000
  G1 X5 Y5 F8000
  G92 E0
  G0 Z0.3 F4000
  G1 X5 X55 E28 F500
  G1 E-2 F3000
  G92 E0
  G1 X70 F40000



#####################################################################
#	LED Macros
#####################################################################
# gelb
[gcode_macro LED_Homing]
gcode:
  SET_LED LED=Leds RED=1.00 GREEN=1.00 BLUE=0.00
	
# orange
[gcode_macro LED_Leveling]
gcode:
  SET_LED LED=Leds RED=1.00 GREEN=0.40 BLUE=0.00
	
# rot
[gcode_macro LED_Heating]
gcode:
	SET_LED LED=Leds RED=1.00 GREEN=0.00 BLUE=0.00
	
# weiß
[gcode_macro LED_Printing]
gcode:
  SET_LED LED=Leds RED=1.00 GREEN=1.00 BLUE=1.00

# dunkles weiß
[gcode_macro LED_Idle]
gcode:
  SET_LED LED=Leds RED=0.60 GREEN=0.60 BLUE=0.60
	
# leichtes grün
[gcode_macro LED_Finish]
gcode:
  SET_LED LED=Leds RED=0.70 GREEN=1.00 BLUE=0.70

# off
[gcode_macro LED_off]
gcode:
  SET_LED LED=Leds RED=0.00 GREEN=0.00 BLUE=0.00




#####################################################################
#	Replacement Macros for Temperature GCodes
#####################################################################

#[gcode_macro SET_HEATER_TEMPERATURE]
#rename_existing : S_H_T
#description     : include LEDs in SET_HEATER_TEMPERATURE 
#gcode:
#  M117     Set temperature { rawparams }
#	SET_LED LED=Leds RED=0.70 GREEN=0.10 BLUE=0.0
#  S_H_T { rawparams }

#####################################################################
#	LED Control
#####################################################################

## Normales LED Licht über einen PIN
#[output_pin caselight ]
##  Chamber Lighting - In 5V-RGB Position
#pin: PD3
#pwm: true
#shutdown_value: 0
#value:100
#cycle_time: 0.01

######################################################################
# Filament Change
######################################################################

# M600: Filament Change. This macro will pause the printer, move the
# tool to the change position, and retract the filament 50mm. Adjust
# the retraction settings for your own extruder. After filament has
# been changed, the print can be resumed from its previous position
# with the "RESUME" gcode.

[pause_resume]

[gcode_macro M600]
gcode:
    {% set X = params.X|default(50)|float %}
    {% set Y = params.Y|default(0)|float %}
    {% set Z = params.Z|default(10)|float %}
    SAVE_GCODE_STATE NAME=M600_state
    PAUSE
    G91
    G1 E-.8 F2700
    G1 Z{5}
    G90
    G1 X{100} Y{10} F3000
    G91
    G1 E-50 F1000
    RESTORE_GCODE_STATE NAME=M600_state

######################################################################
# Preheat
######################################################################

[gcode_macro _PREHEAT]
gcode:

  RESPOND MSG="PREHEAT BED 50 HOTEND 150"
 LED_Heating                                                ; LED HEATING
 SET_HEATER_TEMPERATURE HEATER=heater_bed TARGET=50         ; Preheat Bed 50 Grad
 SET_HEATER_TEMPERATURE HEATER=extruder TARGET=150          ; Preheat Hotend 150 Grad


######################################################################
# G28
######################################################################

[gcode_macro _CG28]

gcode:
    {% if "xyz" not in printer.toolhead.homed_axes %}
        G28
    {% endif %}

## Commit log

2023-03-18 Add files via upload
    Board Mellow E3 ProV3 Doku:
    https://teamgloomy.github.io/fly_e3_pro_v3_general.html
2023-03-18 Add files via upload
    Hardware Info Board
2023-03-18 Add files via upload
    Wireing Fans
2023-03-18 Add files via upload
    DC 12 V board
2023-03-18 Add files via upload
    Wireing SSR bed
2023-03-18 Add files via upload
    wireing Hotend
2023-03-18 Add files via upload
    Stepper wireing
2023-03-18 Add files via upload
    wireing endstop
2023-03-18 Add files via upload
    wireing ADXL
2023-03-18 Add files via upload
    all wireing
2023-03-18 Add files via upload
    Für PI und SSR
    [Pi_SSR_pusher.stl]
2023-03-18 Add files via upload
    SSR Cover
    [ssr cover.stl]
2023-03-18 Add files via upload
    Y and X Endstop
2023-03-21 Create Wireing Schaltplaene
2023-03-21 Create Printsetting
2023-03-22 Update and rename Printsetting to Printersetting
